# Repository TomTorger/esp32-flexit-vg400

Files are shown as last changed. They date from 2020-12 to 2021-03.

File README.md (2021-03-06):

# Flexit SP 30

This project connects an esp32 to a VG400 central ventilation unit from Flexit, measures the temperatures of incoming and exiting air, and regulate the ventilation based on the readings of Radon, CO2, VOC, and humidity.

The project is still in progress. I blew a relay on the main board during this project and I suspect that the resistor for the relay controlling "high" fan speed might be too small.

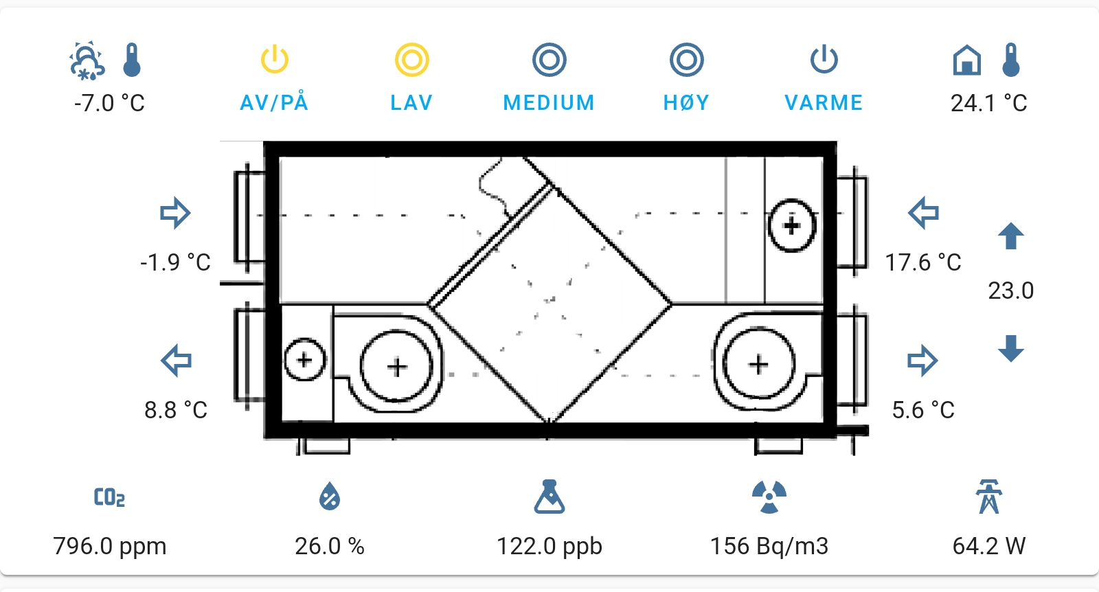
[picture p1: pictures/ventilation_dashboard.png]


### Implementation for esp32 and Home Assistant

#### ESP 32 module
 - esp32
 - [SP425 controller board](https://www.flexit.no/produkter/ventilasjonsaggregat_bolig/automatikk_utgatte_modeller/styresystem_sp_30/)
 - 3x3V [relays] (https://www.aliexpress.com/item/32963196636.html?spm=a2g0s.9042311.0.0.27424c4dnUIR03)
 - 3x [optocouplers](https://www.aliexpress.com/item/32833204725.html?spm=a2g0s.12269583.0.0.ca892879PIkUG4)
 - Network cable (RJ45)
 - [Prototyping board] (https://www.aliexpress.com/item/32944526042.html?spm=a2g0s.9042311.0.0.27424c4deBLnzu)
 - 4x [Dallas thermometers] (https://www.aliexpress.com/item/32523899337.html?spm=a2g0s.9042311.0.0.27424c4d34b0Tb)
 - 3x 1kOhm resistors
 - 2x 2kOhm resistors
 - 1x 4kOhm resistor
 - Wires

#### Other
  - Smart-plug https://www.aliexpress.com/item/4000478798085.html?spm=a2g0s.9042311.0.0.27424c4dHoTBiU
  - CO2, Radon, VOC, humidity sensor [Airthings Wave plus] https://www.airthings.com/en/wave-plus
  - Intel nuc i5
  - 
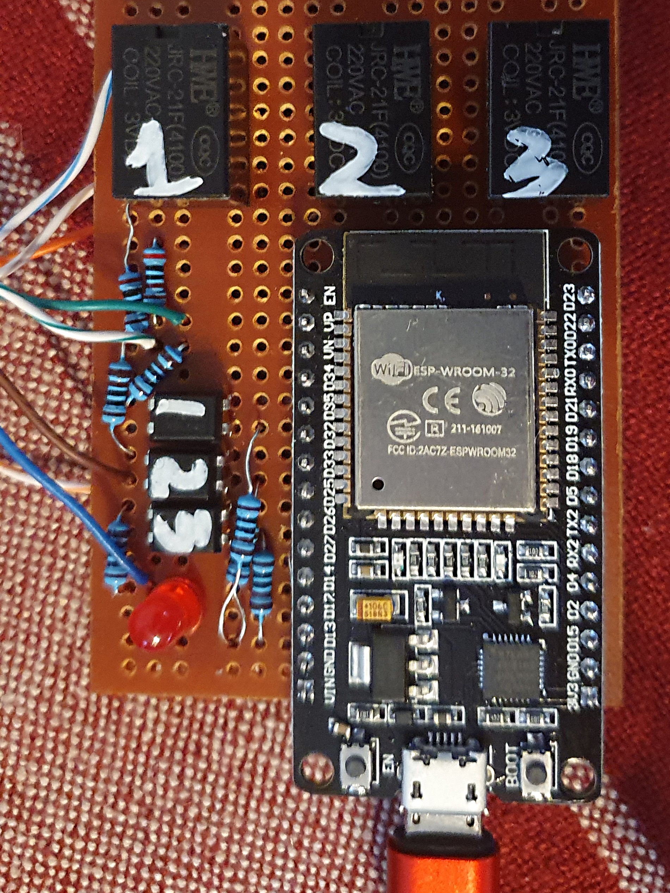
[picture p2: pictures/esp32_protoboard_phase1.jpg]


### Software
 - Home Assistant running in docker container
 - Esphome running in docker container
 - NodeRed running in docker container

### Build instructions:

This image is from the original project and is not absolutely correct. Follow the instructions below


Connect the three 3 V relays to the ESP32:
- Pin 18: to relay 1 in
- Pin 19: to relay 2 in
- Pin 21: to relay 3 in
- ESP32 GND to relay GND-in

Connect the RJ45 wire to the protoboard. The pin numbers correspond to the pin numbers on the VG400 control board:
- wire pin 3: to a diode, and then to relay 3 out
- wire pin 3: with a 1 kΩ resistor to optocoupler 3 input 
- wire pin 4: to relay 1,2,3 GND-out
- wire pin 5: to a 2.2 kΩ resistor, and then to relay 1 out
- wire pin 5: with a 1 kΩ resistor to optocoupler 1 input 
- wire pin 6: to a 2.2 kΩ resistor, and then to relay 2 out
- wire pin 6: with a 1 kΩ resistor to optocoupler 2 input 
- wire pin 7: to optocoupler 1,2,3 GND-in 

Connect the three optocouplers to the ESP32
- Pin 32 to optocoupler 1 out
- Pin 33 to optocoupler 2 out
- Pin 26 to optocoupler 3 out
- optocoupler 1,2,3 GND-out: with 1 kΩ resistors to ESP23 GND

Connect the four DS18B20 temperature sensors to the ESP32:
- Pin 4 to DS18B20 data pin
- 4.7 kΩ pullup resistor for DS18B20 data pin
- 5V to DS18B20 5V pins
- ESP32 GND to DS18B20 GND pins

Connect power to the ESP32:
- Z-UNO, USB: power source
- Z-UNO, GND

### Firmware
Adjust and compile the esphome.yaml in and esphome instance. Download the binaries and flash it to the esp32 with a flashing tool. Subsequent flashing can then be performed Over The Air/network (OTA).

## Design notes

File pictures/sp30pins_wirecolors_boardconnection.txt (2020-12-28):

This assumes that one uses an ordinary network calble to connect from the esp32 board to the sp30 board.
The network cable has stiped and non-striped versions of blue, orange, green, and brown.

Pin 1 - Orange     - Not used
Pin 2 - 1/2 Orange - Not used
Pin 3 - Blue
	  - Connected to a 1kOmh resistor and then to optocoupler 3 in
	  - Connected to a diode and then to relay 3 out
	Function:
Pin 4 - 1/2 Blue
	  - Connected to 1,2,3 ground out
	  Function: This is the ground of the live wires which are used to register a pushed button
Pin 5 - Green
	  - Connected to a 2.2 kOhm resistor and then to relay 2 out
	  - Connected to a 1 kOhm resistor ant then to optocoupler 2 in
	  Function:
Pin 6 1/2 Green
	  - Connected to a 2.2 kOhm resistor and then to relay 2 out
	  - Connected to a 1 kOhm resistor ant then to optocoupler 2 in
	   Function 
Pin 7 - Brown
	  - Connected to optocoupler ground in
      Function: Provide negative pole for the optocoupler
Pin 8 - 1/2 Brown Not used

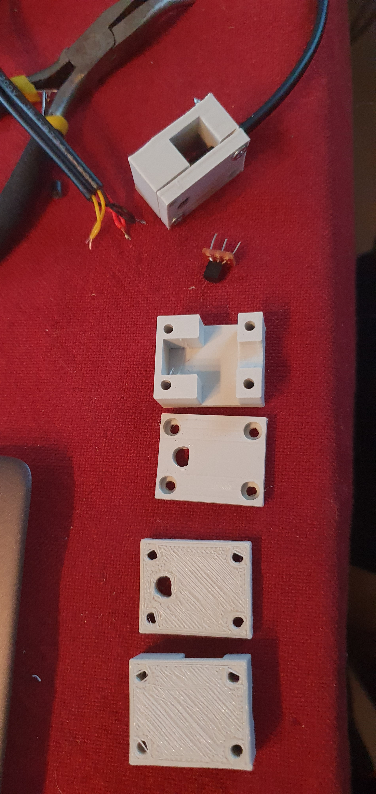
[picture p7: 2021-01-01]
pictures/3dprinted_dallas_holders_w_gap_for_strips.jpg

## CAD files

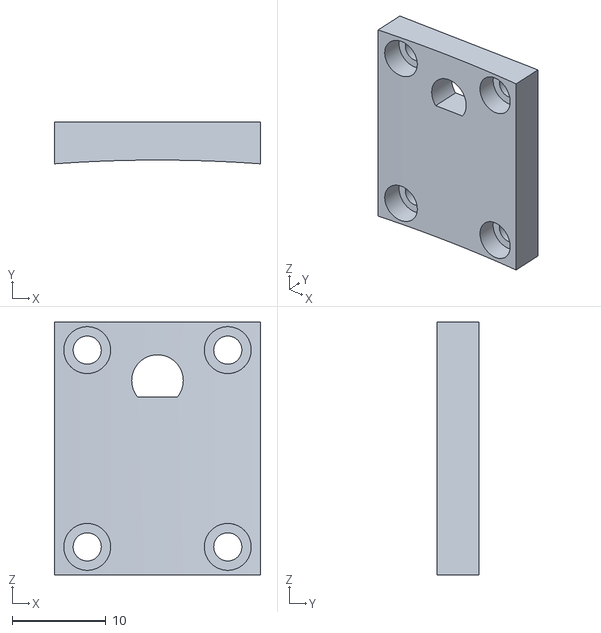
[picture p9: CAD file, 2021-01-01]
3d-print/DallasSensorHolder/dallas_holder.stl
22.0 x 4.45 x 27.0

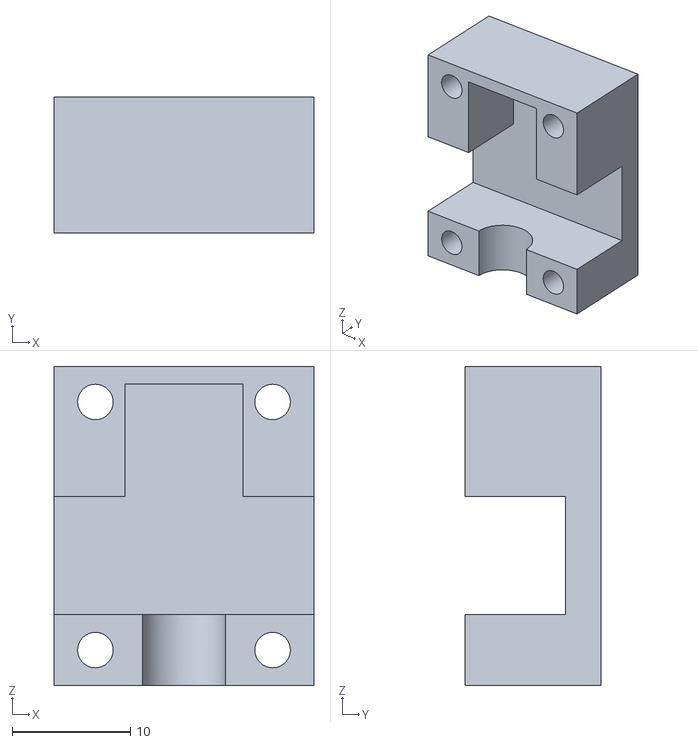
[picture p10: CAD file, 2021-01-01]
3d-print/DallasSensorHolder/dallas_holder_lid.stl
22.0 x 11.5 x 27.0

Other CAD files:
3d-print/DallasSensorHolder/dallas_holder.ipt

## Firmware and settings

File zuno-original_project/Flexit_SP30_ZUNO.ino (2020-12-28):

#include "ZUNO_DS18B20.h"
#include "EEPROM.h"

#define DEBUG_x

#define RELAY_1_PIN                 9
#define RELAY_2_PIN                 10
#define RELAY_3_PIN                 11
#define DS18B20_BUS_PIN             12
#define FAN_LEVEL_1_PIN             A1
#define FAN_LEVEL_2_PIN             A2
#define HEATING_PIN                 A3
#define LED_PIN                     LED_BUILTIN

#define MIN_UPDATE_DURATION         30000
#define MIN_STATE_UPDATE_DURATION   1000
#define MIN_TEMP_UPDATE_DURATION    30000
#define LED_BLINK_DURATION          25

OneWire ow(DS18B20_BUS_PIN);
DS18B20Sensor ds18b20(&ow);

#define MAX_TEMP_SENSORS            4
#define ADDR_SIZE                   8
byte addresses[ADDR_SIZE * MAX_TEMP_SENSORS];
#define ADDR(i) (&addresses[i * ADDR_SIZE])
byte temp_sensors;
word temperature[MAX_TEMP_SENSORS];
word temperatureReported[MAX_TEMP_SENSORS];
word temperatureCalibration[MAX_TEMP_SENSORS];

byte mode = 1;
byte modeChanged = 0;
unsigned long lastSetMode = 0;
byte lastFanLevel = 1;
byte lastFanLevelReported = 99;
byte lastHeating = 0;
byte lastHeatingReported = 99;

unsigned long relayTimer = 0;
unsigned long fanLevelTimer = 0;
unsigned long fanLevelTimer2 = 0;
unsigned long heatingTimer = 0;
unsigned long heatingTimer2 = 0;
unsigned long temperatureTimer[MAX_TEMP_SENSORS];
unsigned long ledTimer = 0;
unsigned long listConfigTimer = 0;

word status_report_interval_config;
word temperature_report_interval_config;
word temperature_report_threshold_config;
word relay_duration_config;
word enabled_config;
word enabled_mode_config;
word default_config_set_config;

ZUNO_SETUP_SLEEPING_MODE(ZUNO_SLEEPING_MODE_ALWAYS_AWAKE);
ZUNO_SETUP_PRODUCT_ID(0xC0, 0xC0);
ZUNO_SETUP_CFGPARAMETER_HANDLER(config_parameter_changed);

ZUNO_SETUP_CHANNELS(
    ZUNO_SWITCH_MULTILEVEL(getterMode, setterMode),

    ZUNO_SENSOR_MULTILEVEL(ZUNO_SENSOR_MULTILEVEL_TYPE_GENERAL_PURPOSE_VALUE,
        SENSOR_MULTILEVEL_SCALE_PERCENTAGE_VALUE,
        SENSOR_MULTILEVEL_SIZE_ONE_BYTE,
        SENSOR_MULTILEVEL_PRECISION_ZERO_DECIMALS,
        getterFanLevel),

    ZUNO_SENSOR_MULTILEVEL(ZUNO_SENSOR_MULTILEVEL_TYPE_GENERAL_PURPOSE_VALUE,
        SENSOR_MULTILEVEL_SCALE_PERCENTAGE_VALUE,
        SENSOR_MULTILEVEL_SIZE_ONE_BYTE,
        SENSOR_MULTILEVEL_PRECISION_ZERO_DECIMALS,
        getterHeating),

    ZUNO_SENSOR_MULTILEVEL(ZUNO_SENSOR_MULTILEVEL_TYPE_TEMPERATURE,
        SENSOR_MULTILEVEL_SCALE_CELSIUS,
        SENSOR_MULTILEVEL_SIZE_TWO_BYTES,
        SENSOR_MULTILEVEL_PRECISION_TWO_DECIMALS,
        getterTemp1),

    ZUNO_SENSOR_MULTILEVEL(ZUNO_SENSOR_MULTILEVEL_TYPE_TEMPERATURE,
        SENSOR_MULTILEVEL_SCALE_CELSIUS,
        SENSOR_MULTILEVEL_SIZE_TWO_BYTES,
        SENSOR_MULTILEVEL_PRECISION_TWO_DECIMALS,
        getterTemp2),

    ZUNO_SENSOR_MULTILEVEL(ZUNO_SENSOR_MULTILEVEL_TYPE_TEMPERATURE,
        SENSOR_MULTILEVEL_SCALE_CELSIUS,
        SENSOR_MULTILEVEL_SIZE_TWO_BYTES,
        SENSOR_MULTILEVEL_PRECISION_TWO_DECIMALS,
        getterTemp3),

    ZUNO_SENSOR_MULTILEVEL(ZUNO_SENSOR_MULTILEVEL_TYPE_TEMPERATURE,
        SENSOR_MULTILEVEL_SCALE_CELSIUS,
        SENSOR_MULTILEVEL_SIZE_TWO_BYTES,
        SENSOR_MULTILEVEL_PRECISION_TWO_DECIMALS,
        getterTemp4)
);

void setterMode(byte value) {
    mode = value;
    modeChanged = 1;
    lastSetMode = millis();
}

byte getterMode(void) {
    return mode;
}

byte getterFanLevel(void) {
  return lastFanLevel;
}

byte getterHeating(void) {
  return lastHeating;
}

word getterTemp1() {
    return temperature[0];
}

word getterTemp2() {
    return temperature[1];
}

word getterTemp3() {
    return temperature[2];
}

word getterTemp4() {
    return temperature[3];
}

void config_parameter_changed(byte param, word value) {
    if (param == 64) {
        status_report_interval_config = value;
    }
    if (param == 65) {
        temperature_report_interval_config = value;
    }
    if (param == 66) {
        temperature_report_threshold_config = value;
    }
    if (param == 67) {
        relay_duration_config = value;
    }
    if (param == 68) {
        enabled_config = value;
        if (enabled_config < 0 || enabled_config > 1) {
            enabled_config = 0;
        }
    }
    if (param == 69) {
        enabled_mode_config = value;
        if (enabled_mode_config < 0 || enabled_mode_config > 1) {
            enabled_mode_config = 0;
        }
    }
    if (param >= 70 && param <= 73) {
        temperatureCalibration[param - 70] = value;
    }

#ifdef DEBUG
    Serial.print("config ");
    Serial.print(param);
    Serial.print(" = ");
    Serial.println(value);
#endif
}

void setup() {
    pinMode(RELAY_1_PIN, OUTPUT);
    pinMode(RELAY_2_PIN, OUTPUT);
    pinMode(RELAY_3_PIN, OUTPUT);
    digitalWrite(RELAY_1_PIN, HIGH);
    digitalWrite(RELAY_2_PIN, HIGH);
    digitalWrite(RELAY_3_PIN, HIGH);
    pinMode(LED_PIN, OUTPUT);

    pinMode(FAN_LEVEL_1_PIN, INPUT_PULLUP);
    pinMode(FAN_LEVEL_2_PIN, INPUT_PULLUP);
    pinMode(HEATING_PIN, INPUT_PULLUP);

    Serial.begin();
    fetchConfig();
    temp_sensors = ds18b20.findAllSensors(addresses);
    fetchMode();
}

void fetchConfig() {
    status_report_interval_config = zunoLoadCFGParam(64);
    temperature_report_interval_config = zunoLoadCFGParam(65);
    temperature_report_threshold_config = zunoLoadCFGParam(66);
    relay_duration_config = zunoLoadCFGParam(67);
    enabled_config = zunoLoadCFGParam(68);
    enabled_mode_config = zunoLoadCFGParam(69);
    for (byte i = 0; i < MAX_TEMP_SENSORS; i++) {
        temperatureCalibration[i] = zunoLoadCFGParam(70 + i);
    }

    default_config_set_config = zunoLoadCFGParam(96);
    if (default_config_set_config != 1) {
        status_report_interval_config = 600;
        zunoSaveCFGParam(64, status_report_interval_config);

        temperature_report_interval_config = 600;
        zunoSaveCFGParam(65, temperature_report_interval_config);

        temperature_report_threshold_config = 20;
        zunoSaveCFGParam(66, temperature_report_threshold_config);

        relay_duration_config = 250;
        zunoSaveCFGParam(67, relay_duration_config);

        enabled_config = 0;
        zunoSaveCFGParam(68, enabled_config);

        enabled_mode_config = 0;
        zunoSaveCFGParam(69, enabled_mode_config);

        for (byte i = 0; i < MAX_TEMP_SENSORS; i++) {
            temperatureCalibration[i] = 0;
            zunoSaveCFGParam(70 + i, temperatureCalibration[i]);
        }

        default_config_set_config = 1;
        zunoSaveCFGParam(96, default_config_set_config);
    }
}

void fetchMode() {
    dword addr = 0x800;
    mode = EEPROM.read(addr);
    if (mode < 1 || mode > 13) {
        mode = 1;
    }
    modeChanged = 1;
    zunoSendReport(1);
}

void storeMode() {
    dword addr = 0x800;
    EEPROM.write(addr, mode);
}

void ledBlink(unsigned long timerNow) {
    ledTimer = timerNow;
    digitalWrite(LED_PIN, HIGH);
}

void ledBlinkOff(unsigned long timerNow) {
    if (ledTimer > 0 && (timerNow - ledTimer > LED_BLINK_DURATION)) {
        ledTimer = 0;
        digitalWrite(LED_PIN, LOW);
    }
}

void loop() {
    if (enabled_config == 1) {
        unsigned long timerNow = millis();
        if (enabled_mode_config == 1) {
            handleMode(timerNow);
        }
        getFanLevel(timerNow);
        getHeating(timerNow);
        reportFanLevel(timerNow);
        ledBlinkOff(timerNow);
        reportHeating(timerNow);
        ledBlinkOff(timerNow);
        reportTemperatures(timerNow);
        ledBlinkOff(timerNow);
#ifdef DEBUG
        listConfig(timerNow);
#endif
    }
}

void handleMode(unsigned long timerNow) {
    if ((modeChanged == 1) && ((timerNow - relayTimer) > relay_duration_config)) {
        relayTimer = timerNow;
        ledBlink(timerNow);

        byte r1 = ((mode % 10) == 2) ? LOW : HIGH;
        digitalWrite(RELAY_1_PIN, r1);

        byte r2 = ((mode % 10) == 3) ? LOW : HIGH;
        digitalWrite(RELAY_2_PIN, r2);

        byte r3 = ((mode - mode % 10) == 10) ? LOW : HIGH;
        digitalWrite(RELAY_3_PIN, r3);

        storeMode();
        modeChanged = 0;
        delay(25);

#ifdef DEBUG_3
        Serial.print(timerNow / 1000);
        Serial.print(": r1: ");
        Serial.print(r1);
        Serial.print(", r2: ");
        Serial.print(r2);
        Serial.print(", r3: ");
        Serial.println(r3);
#endif
    }
}

void getFanLevel(unsigned long timerNow) {
    int fl1 = digitalRead(FAN_LEVEL_1_PIN);
    int fl2 = digitalRead(FAN_LEVEL_2_PIN);
    lastFanLevel = fl1 == 1 && fl2 == 0 ? 3 : (fl1 == 0 && fl2 == 1 ? 2 : 1);

#ifdef DEBUG_2
    if (timerNow - fanLevelTimer2 > 2000) {
        fanLevelTimer2 = timerNow;
        Serial.print(timerNow / 1000);
        Serial.print(": fl1: ");
        Serial.print(fl1);
        Serial.print(", fl2: ");
        Serial.println(fl2);
        Serial.print(", fan level: ");
        Serial.print(lastFanLevel);
        Serial.print(", mode: ");
        Serial.println(mode);
    }
#endif
}

void getHeating(unsigned long timerNow) {
    int heat = digitalRead(HEATING_PIN);
    lastHeating = heat == 0 ? 10 : 0;

#ifdef DEBUG_2
    if (timerNow - heatingTimer2 > 2000) {
        heatingTimer2 = timerNow;
        Serial.print(timerNow / 1000);
        Serial.print(", heat: ");
        Serial.print(heat);
        Serial.print(", heating: ");
        Serial.print(lastHeating);
        Serial.print(", mode: ");
        Serial.println(mode);
    }
#endif
}

void reportFanLevel(unsigned long timerNow) {
    bool changed = lastFanLevel != lastFanLevelReported;
    unsigned long timer1Diff = timerNow - lastSetMode;
    unsigned long timer2Diff = timerNow - fanLevelTimer;
    unsigned long repInterval = ((unsigned long)status_report_interval_config) * 1000;

    if (changed && timer1Diff > MIN_STATE_UPDATE_DURATION || timer2Diff > repInterval) {
        lastFanLevelReported = lastFanLevel;
        fanLevelTimer = timerNow;
        ledBlink(timerNow);
        zunoSendReport(2);
#ifdef DEBUG_4
        Serial.print(timerNow / 1000);
        Serial.print(": lastFanLevel: ");
        Serial.println(lastFanLevel);
#endif
    }
}

void reportHeating(unsigned long timerNow) {
    bool changed = lastHeating != lastHeatingReported;
    unsigned long timer1Diff = timerNow - lastSetMode;
    unsigned long timer2Diff = timerNow - heatingTimer;
    unsigned long repInterval = ((unsigned long)status_report_interval_config) * 1000;

    if (changed && timer1Diff > MIN_STATE_UPDATE_DURATION || timer2Diff > repInterval) {
        lastHeatingReported = lastHeating;
        heatingTimer = timerNow;
        ledBlink(timerNow);
        zunoSendReport(3);
#ifdef DEBUG_4
        Serial.print(timerNow / 1000);
        Serial.print(": lastHeating: ");
        Serial.println(lastHeating);
#endif
    }
}

void reportTemperatures(unsigned long timerNow) {
    for (byte i = 0; i < temp_sensors && i < MAX_TEMP_SENSORS; i++) {

        unsigned long timerDiff = timerNow - temperatureTimer[i];
        unsigned long repInterval = ((unsigned long)temperature_report_interval_config) * 1000;

        if (timerDiff > MIN_TEMP_UPDATE_DURATION || timerDiff > repInterval) {

            temperature[i] = ((word)(ds18b20.getTemperature(ADDR(i)) * 100)) + temperatureCalibration[i];
            bool changed = temperature[i] > temperatureReported[i] + temperature_report_threshold_config || temperature[i] < temperatureReported[i] - temperature_report_threshold_config;

            if (changed && timerDiff > MIN_TEMP_UPDATE_DURATION || timerDiff > repInterval) {
                temperatureTimer[i] = timerNow;
                temperatureReported[i] = temperature[i];
                ledBlink(timerNow);
                zunoSendReport(i + 4);
#ifdef DEBUG_3
                Serial.print(timerNow / 1000);
                Serial.print(": temp[");
                Serial.print(i);
                Serial.print("]: ");
                Serial.println(temperature[i]);
#endif
            }
        }
    }
}

#ifdef DEBUG
void listConfig(unsigned long timerNow) {
    if (timerNow - listConfigTimer > MIN_UPDATE_DURATION) {
        listConfigTimer = timerNow;
        Serial.print("status_report_interval_config: ");
        Serial.println(status_report_interval_config);
        Serial.print("temperature_report_interval_config: ");
        Serial.println(temperature_report_interval_config);
        Serial.print("temperature_report_threshold_config: ");
        Serial.println(temperature_report_threshold_config);
        Serial.print("relay_duration_config: ");
        Serial.println(relay_duration_config);
        Serial.print("enabled_config: ");
        Serial.println(enabled_config);
        Serial.print("enabled_mode_config: ");
        Serial.println(enabled_mode_config);
        Serial.print("temp sensors: ");
        Serial.println(temp_sensors);
        for (byte i = 0; i < MAX_TEMP_SENSORS; i++) {
            Serial.print("temperatureCalibration[");
            Serial.print(i);
            Serial.print("]: ");
            Serial.println(temperatureCalibration[i]);
        }
    }
}
#endif
